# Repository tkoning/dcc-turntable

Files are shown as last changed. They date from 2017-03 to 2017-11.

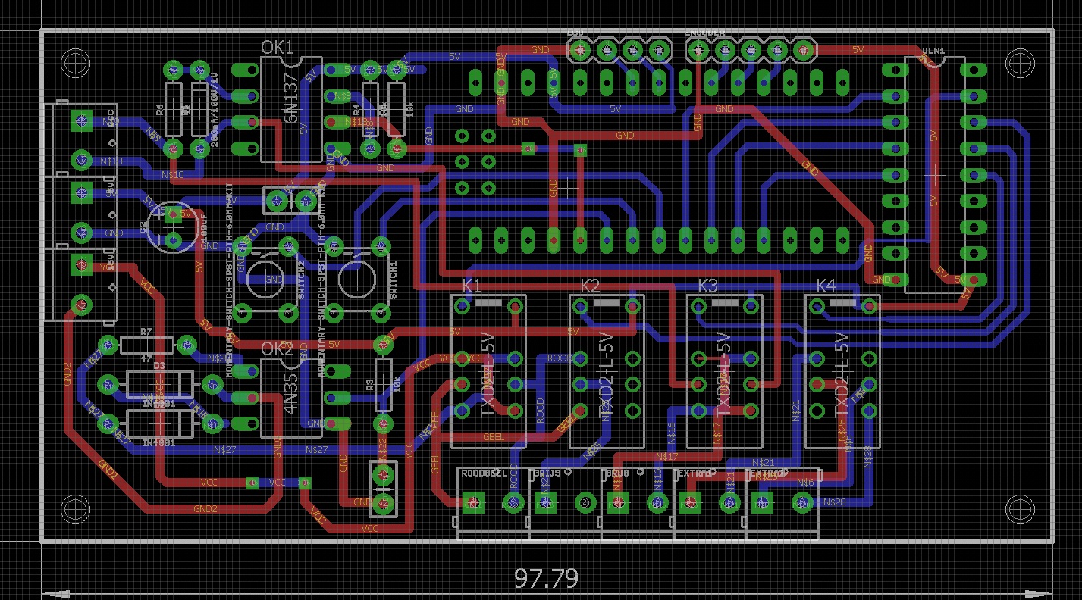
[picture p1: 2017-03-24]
print draaischijf decoder3.jpg

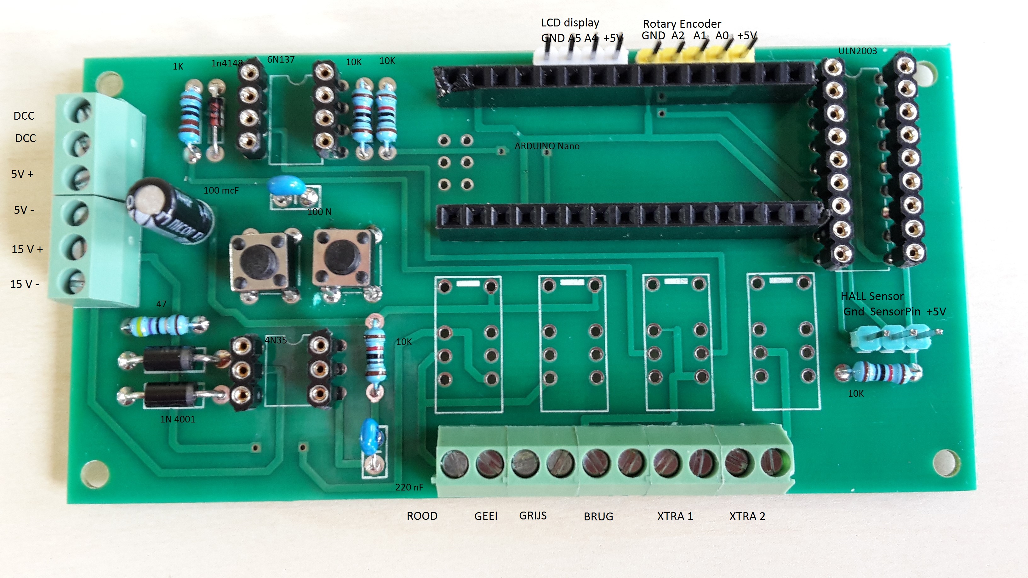
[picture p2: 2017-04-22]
legenda print.jpg

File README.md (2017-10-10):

# dcc-turntable
DCC control of a fleischmann turntable

Digital control of a fleischmann turntable can be achieved with an arduino nano

No modification of the original turntable is needed.
The turntable is controlled by four relays, 

DCC input is by means of the standard mynabay optocoupler circuit.
Manual Control is by means of a rotary encoder and an LCD display.

For indexing of the fleischmann turntable a power sensing circuit is used.
A seperate relais can be used to "flip" the polarity of the turntable brige.

code is annotated in dutch.

the turntable can be seen  in action on youtube.

https://www.youtube.com/watch?v=R1SMiSs2mZU

https://www.youtube.com/watch?v=gE1vPq5jKME

https://www.youtube.com/watch?v=S2jX1PM-Gi4

Schematic of the decoder is in the repository.

New software version 6 : position of bridge is retained at arduino shutdown by setting eeprom parameter in code

erratum : relay's must de mounted on the bottomside of the printed circuit board due to a design mistake regarding polarity of the relay coil.  Increase resitor r6 (dcc optocoupler circuit to 4,7 k)

I have noticed the fleischmann turntable electric engine to be unreliable. Especialy when cold the engine can cause short circuits
A new software version (vs10) cuts the power after a 3 second period
For this to work the positive power line has to be connected via the spare connecors of the aux1 relais

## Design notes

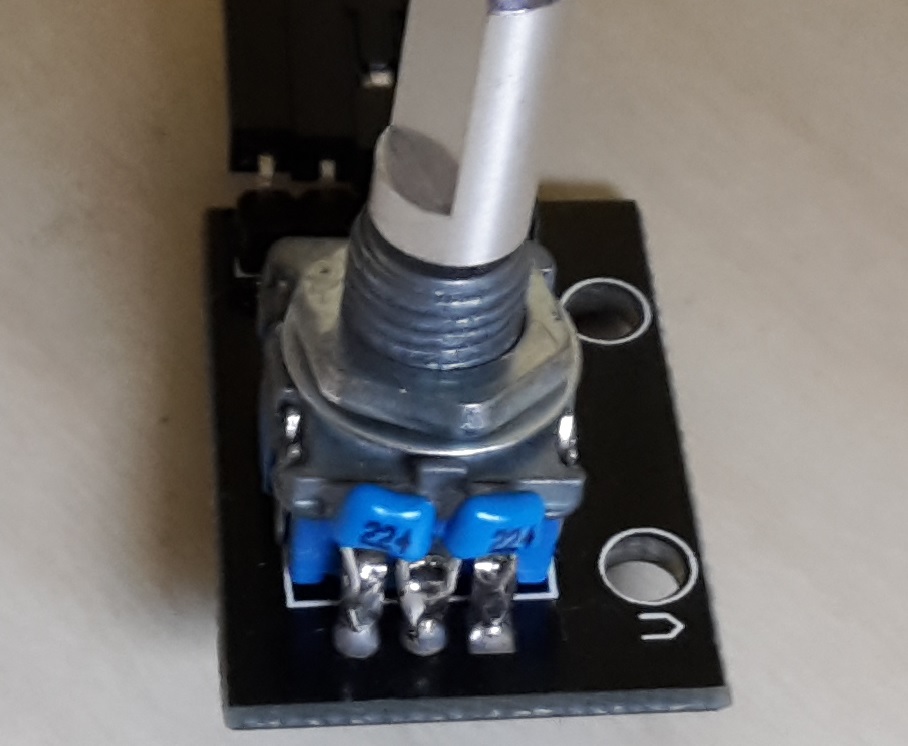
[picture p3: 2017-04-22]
encoder.jpg

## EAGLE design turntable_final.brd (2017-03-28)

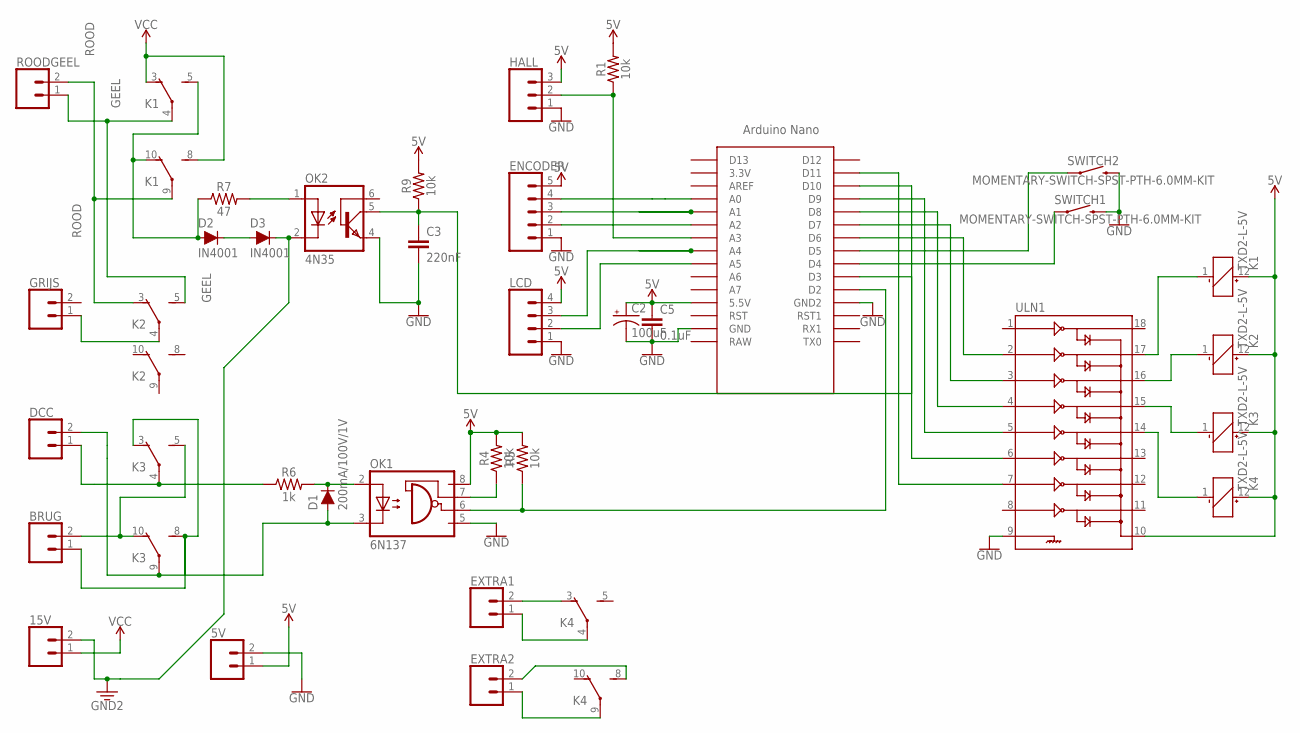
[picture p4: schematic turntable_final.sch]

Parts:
5V, 15V: CONN_023.5MM_LOCK; SCREWTERMINAL-3.5MM-2_LOCK
BRUG: CONN_023.5MM_LOCK; SCREWTERMINAL-3.5MM-2_LOCK
C2: 100uF; CPOL-RADIAL-2.5MM-5MM
C3: 220nF; CAP-PTH-SMALL-KIT
C5: 0.1uF; CAP-PTH-SMALL-KIT
D1: 200mA/100V/1V; DIODE-1N4148
D2, D3: IN4001; DIODE-1N4001
DCC: CONN_023.5MM_LOCK; SCREWTERMINAL-3.5MM-2_LOCK
ENCODER: CONN_05; 1X05
EXTRA1, EXTRA2: CONN_023.5MM_LOCK; SCREWTERMINAL-3.5MM-2_LOCK
GRIJS: CONN_023.5MM_LOCK; SCREWTERMINAL-3.5MM-2_LOCK
HALL: CONN_03; 1X03
K1, K2, K3, K4: TXD2-L-5V; TXD2
LCD: CONN_04; 1X04
OK1: 6N137; DIL08
OK2: 4N35; DIL06
R1, R4, R5, R9: 10k; AXIAL-0.3
R6: 1k; AXIAL-0.3
R7: 47; AXIAL-0.3
ROODGEEL: CONN_023.5MM_LOCK; SCREWTERMINAL-3.5MM-2_LOCK
SWITCH1, SWITCH2: MOMENTARY-SWITCH-SPST-PTH-6.0MM-KIT; TACTILE_SWITCH_PTH_6.0MM_KIT
U$1: NANO
ULN1: ULN2803DIP; DIL18

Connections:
5V: 5V.1, C2.1 (+), C5.1, ENCODER.5, HALL.3, K1.12 (+), K2.12 (+), K3.12 (+), K4.12 (+), LCD.4, OK1.8 (VCC), R1.P$2 (2), R4.P$2 (2), R5.P$2 (2), R9.P$2 (2), U$1.5V (5.5V), ULN1.10
GEEL: K1.4, K2.5 (S), ROODGEEL.1
GND: 5V.2, C2.2 (-), C3.2, C5.2, ENCODER.1, HALL.1, LCD.1, OK1.5 (GND), OK2.4 (EMI), SWITCH1.3 (2), SWITCH2.3 (2), U$1.GND, U$1.GND1 (GND2), ULN1.9
GND2: 15V.2, D3.C, OK2.2 (C)
unnamed: HALL.2, R1.P$1 (1), U$1.A3
unnamed: K3.1 (-), ULN1.15
unnamed: K1.1 (-), ULN1.17
unnamed: ENCODER.3, U$1.A1
unnamed: EXTRA2.1, K4.9
unnamed: K4.1 (-), ULN1.14
unnamed: OK1.7 (VE), R4.P$1 (1)
unnamed: DCC.1, K3.4, R6.P$1 (1)
unnamed: D1.A, DCC.2, K3.9, OK1.3 (C)
unnamed: ENCODER.4, U$1.A0
unnamed: K2.1 (-), ULN1.16
unnamed: OK1.6 (VO), R5.P$1 (1), U$1.D2
unnamed: D1.C, OK1.2 (A), R6.P$2 (2)
unnamed: ENCODER.2, U$1.A2
unnamed: BRUG.2, K3.5 (S), K3.10 (O)
unnamed: BRUG.1, K3.3 (O), K3.8 (S)
unnamed: D2.C, D3.A
unnamed: U$1.D10, ULN1.6
unnamed: OK2.1 (A), R7.P$2 (2)
unnamed: EXTRA1.2, K4.3 (O)
unnamed: C3.1, OK2.5 (COL), R9.P$1 (1), U$1.D3
unnamed: SWITCH1.1, U$1.D4
unnamed: SWITCH2.1, U$1.D5
unnamed: GRIJS.1, K2.4
unnamed: EXTRA1.1, K4.4
unnamed: D2.A, K1.5 (S), K1.10 (O), R7.P$1 (1)
unnamed: EXTRA2.2, K4.8 (S)
unnamed: U$1.D9, ULN1.5
unnamed: U$1.D8, ULN1.4
unnamed: U$1.D7, ULN1.3
unnamed: U$1.D6, ULN1.2
unnamed: LCD.3, U$1.A4
unnamed: LCD.2, U$1.A5
unnamed: U$1.D11, ULN1.7
ROOD: K1.9, K2.3 (O), ROODGEEL.2
VCC: 15V.1, K1.3 (O), K1.8 (S)

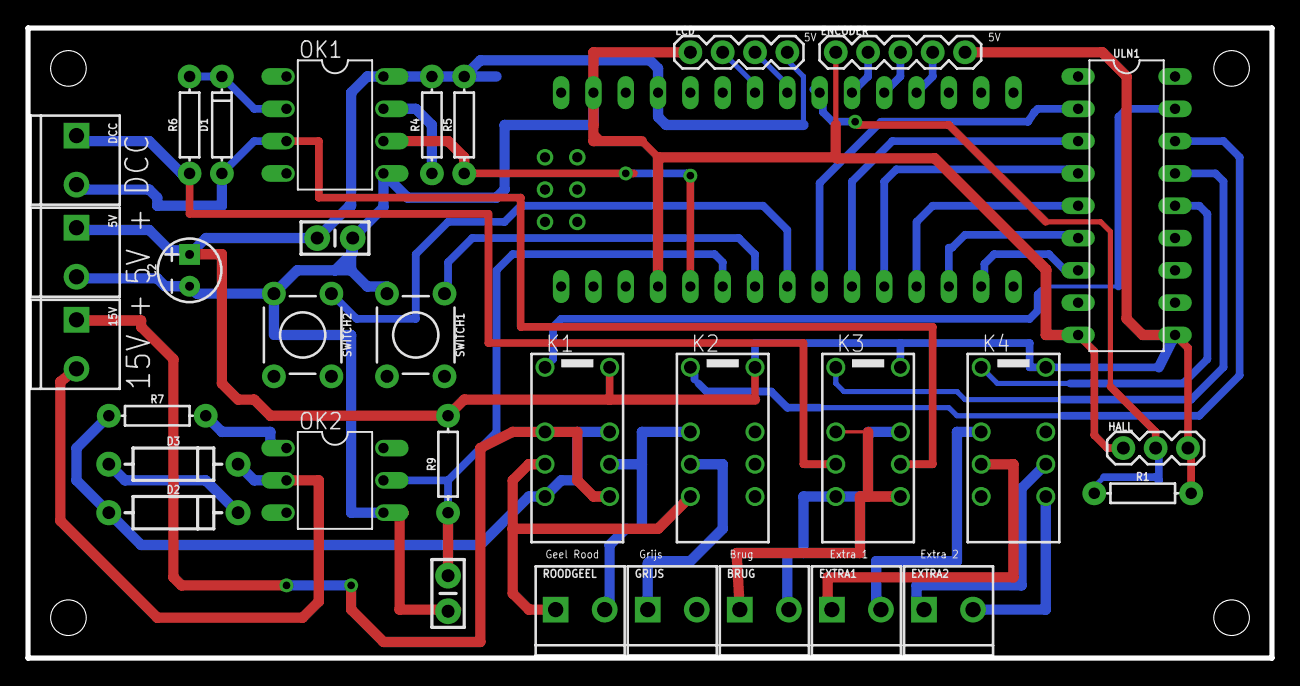
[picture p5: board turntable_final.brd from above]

Board: 2 copper layers, 97.8 x 49.5 mm, 33 parts (0 on the bottom side), 40 nets.

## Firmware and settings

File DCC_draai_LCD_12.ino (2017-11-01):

/*
  //////////////////////////////////////////////////////////////////////////////////////////////////////////////////////
  Arduino DCC Turntable control

  Basis idee  geef korte puls op het locking relais, de draaischijf gaat draaien
  als de draaischijf 1 positie gedraait heeft, stopt de stroom door de motor automatisch
  dit genereert een overgang van laag naar hoog op de motor sense pin
  Gebruik dit event om te bepalen hoeveeel afslagen er gedraaid is en genereer eventueel een nieuwe puls

  versie DCC_draai_lcd10
    inbouwen DCC stuurelementen, eenvoudige koppeling tussen DCC en draaischijf gemaakt
    onderstening van commando'ga naar track nr , + 1 track, -1 track, 180 graden draai
    ondersteuning LCD display
    ondersteuning nieuwe hardware setup met relais sturing via ULN 2803
    aanpassingen tbv nieuw print layout
    gebruik van het EEprom geheugen, de draaischijf onthoudt op welke track de brug stond als het programma wordt afgesloten
    nulling subroutine door het gelijktijdig indrukken van beide print schakelaars
    puls op het aux relais bij het bereiken van de eindpositie
    syntax aanpassingen, variable naamgeving verbeterd
    nog ongeteste beveiliging tegen overbelasting mbv timer in de draairoutine en in main loop
    keuze "nullen" of EEProm geheugen bij het opstarten


  In Rocrail met Xpressnet interface liggen de adressen 4 lager dan de standaard LDT adressen dus basis is 221 ipv 225
  Dit moet worden aangepast met de offset constante
  De Rocrail commando's zijn geinverteerd (instellenin in Rocrail zelf)
  Rocrail genereert 2 commando's een draairichting en een afslagnummer  De draairichting is overbodig en wordt niet gebruikt

  Rotary encoder read example
   https://www.circuitsathome.com/mcu/reading-rotary-encoder-on-arduino/
   niet interupt gebaseerd, afhankelijk van snelheid in de loop
   gebonden aan a0 en a1

  Original DCC sketch : Arduino DCC solenoid Control  Author: Ruud Boer - January 2015
  Adapted for turntable control with LDT protocol Dick Koning feb 2017, echter de nummering van de sporen is conform RocRail

  The DCC signal is optically separated and fed to pin 2 (=Interrupt 0). Schematics: www.mynabay.com
  Many thanks to www.mynabay.com for publishing their DCC monitor and -decoder code.

  Aangepast aan nieuwe motor  (draairichting omgekeerd, tijdconcstante verkleind)


  TODO break statement tijdens daai
  TODO calibratie algoritme

  //////////////////////////////////////////////////////////////////////////////////////////////////////////////////////
*/

#include <DCC_Decoder.h>            // Mynabay DCC library
#define kDCC_INTERRUPT 0

#include <LiquidCrystal_I2C.h>
#include <EEPROM.h>

LiquidCrystal_I2C lcd(0x27, 16, 2); // set the LCD address to 0x27 for a 16 chars and 2 line display

// Pindefinities

const byte dccPin =    2;       // aansluiting DCC signaal
const byte cSense =    3;       // curent sense motoraandrijving
const byte richting =  6;       // Arduino Digital I/O pin number  tbv relais sturing
const byte lock =      7;       // relais wat de interne "lock" van de draaischijf aanstuurt
const byte brug =      8;       // ompoolrelais tbv polariteit van de draaibrug
const byte aux =       9;       // hulp relais bv tbv terugmelding

const byte In_1  =     4;       // Arduino Digital I/O pin number  tbv schakelaars
const byte In_2 =      5;

const byte ENC_A =    14;        //A0   encoder pin A
const byte ENC_B  =   15;        //A1   encoder pin B
const byte ENC_SW =   16;        //A2   encoder switch pin
const byte ledPin =   13;        //ledPin

#define ENC_PORT PINC

// Globale variabelen

int teller = 0;                      // teller is het aantal afslagen dat de schijf moet draaien
int track = 0;                       // actuele afslag waar de draaischijf zich bevindt
int target = 0;                      // doel waarnaar naar toe gedraaid moet worden
byte brugrelais = 0;                 // ompoolrelais draaibrug  Normaal=0 ( NC aansluitingen)  Geinverteerd =1  C aansluitingen
boolean led =     0;

const int EEadres = 100;             // EEadres wordt gebruikt om de track positie vd brug te bewaren
const int EEbrug =  150;             // EEbrug wordt gebruikt om de "stand" van het brugrelais op te slaan
byte EEvalue  =       0;

const boolean aan =    1;
const boolean uit  =   0;
const boolean eeprom = 1;               // eeprom 1 opslag in eeprom,  eeprom  0 geen opslag

const unsigned long pulsDuur = 1500;    // pulsDuur geeft aan hoelang de puls default duurt  Moet iets korter zijn dan de tijd die nodig is voor 1 stap
const unsigned long safeDuur = 3500;    // als de motor langer loopt dan safeDuur stopt de draaischijf automatisch


//////////////////////////////////////////////////////////////////////////////////////////////////////////////////////
// Invulvelden tbv DCC sturing

const int keerA = 12;                 // keerA en keerB zijn de grenzen voor het ompolen van de brug polariteit
const int keerB = 36;

const byte maxaccessories = 6;        // The number of "LDT command" adressen you want to control with this Arduino
const byte offset = 0;                // Offset tov originele LDT adressen  Bij gebruik Xpressnet/ multimouse offset = 4 anders offset = 0

//////////////////////////////////////////////////////////////////////////////////////////////////////////////////////

typedef struct
{
  int               address;          // Address to respond to
  byte              output;           // State of accessory: 1=on, 0=off   rood /groen in wissel commando
  int               track;            // turntable tracknumber
  int               track2;           // turntable track number
  boolean           finished;         // finished : 0=busy 1= ready for next command
  boolean           activate;         // start verwerking commando
  unsigned long     offMilli;         // for internal use
  unsigned long     durationMilli;    // for internal use  "busy periode"

}
DCCAccessoryAddress;
DCCAccessoryAddress accessory[maxaccessories];

//////////////////////////////////////////////////////////////////////////////////////////////////////////////////////
// DCC packet handler
//////////////////////////////////////////////////////////////////////////////////////////////////////////////////////
void BasicAccDecoderPacket_Handler(int address, boolean activate, byte data)
{
  // Convert NMRA packet address format to human address
  address -= 1;
  address *= 4;
  address += 1;
  address += (data & 0x06) >> 1;

  boolean enable = (data & 0x01) ? 1 : 0;

  for (int i = 0; i < maxaccessories; i++)
  {
    if ( address == accessory[i].address )
    {
      accessory[i].activate = 1;
      if ( enable ) {
        accessory[i].output = 1;
      }
      else {
        accessory[i].output = 0;
      }
    }
  }
} // END BasicAccDecoderPacket_Handler


//////////////////////////////////////////////////////////////////////////////////////////////////////////////////////
// Initialization: COPY - PASTE the structure as many times as you have commands and fill in the values you want.
//////////////////////////////////////////////////////////////////////////////////////////////////////////////////////

void ConfigureDecoderFunctions() // The amount of accessories must be same as in line 95 above!
{
  accessory[0].address = 226 - offset; // basisadres LDT =225, eerste commando 226     Voor Multimaus + rocrail  adres -4 invoeren
  accessory[0].track = 0;             // output 0 adres
  accessory[0].track2 = 0;            // output 1 adres    LDT : 226 1 draai 180 graden
  accessory[0].finished = 1;          // Do not change this value
  accessory[0].activate = 0;          // Do not change this value
  accessory[0].output = 0;            // Do not change this value
  accessory[0].durationMilli = 250;

  accessory[1].address = 227 - offset;
  accessory[1].track = 0;             // output 0 adres    LDT : 227 0 draai 1 positie CW
  accessory[1].track2 = 0;            // output 1 adres    LDT : 226 1 draai 1 positie CCW
  accessory[1].finished = 1;          // Do not change this value
  accessory[1].activate = 0;          // Do not change this value
  accessory[1].output = 0;            // Do not change this value
  accessory[1].durationMilli = 250;

  accessory[2].address = 229 - offset;
  accessory[2].track = 0;             // output 0 adres    LDT : 229 ga naar spoor 1
  accessory[2].track2 = 4;            // output 1 adres    LDT : 229 ga naar spoor 2
  accessory[2].finished = 1;          // Do not change this value
  accessory[2].activate = 0;          // Do not change this value
  accessory[2].output = 0;            // Do not change this value
  accessory[2].durationMilli = 250;

  accessory[3].address = 230 - offset;
  accessory[3].track = 6;             // output 0 adres    LDT : 230 ga naar spoor 3
  accessory[3].track2 = 8;           // output 1 adres    LDT : 230 ga naar spoor 4
  accessory[3].finished = 1;          // Do not change this value
  accessory[3].activate = 0;          // Do not change this value
  accessory[3].output = 0;            // Do not change this value
  accessory[3].durationMilli = 250;

  accessory[4].address = 231 - offset;
  accessory[4].track = 24;            // output 0 adres    LDT : 231 ga naar spoor 5
  accessory[4].track2 = 36;           // output 1 adres    LDT : 231 ga naar spoor 6
  accessory[4].finished = 1;          // Do not change this value
  accessory[4].activate = 0;          // Do not change this value
  accessory[4].output = 0;            // Do not change this value
  accessory[4].durationMilli = 250;

  // basisadres LDT =225, eerste commando is programeerstand hier gebruikt als reset, toekomst calibratie oid
  accessory[5].address = 225 - offset;
  accessory[5].track = 0;             // output 0 adres    reset track en target naar 0  moet nog iets in om dat ogv sensor te doen
  accessory[5].track2 = 0;            // output 1 adres    reset track en target naar 0  moet nog iets in om dat ogv sensor te doen
  accessory[5].finished = 1;          // Do not change this value
  accessory[5].activate = 0;          // Do not change this value
  accessory[5].output = 0;            // Do not change this value
  accessory[5].durationMilli = 250;

} // END ConfigureDecoderFunctions



//////////////////////////////////////////////////////////////////////////////////////////////////////////////////////

void setup()
{
  unsigned long timer;
  DCC.SetBasicAccessoryDecoderPacketHandler(BasicAccDecoderPacket_Handler, true);
  ConfigureDecoderFunctions();
  DCC.SetupDecoder( 0x00, 0x00, kDCC_INTERRUPT );


  //-------( Initialize Pins so relays are inactive at reset)----
  digitalWrite(richting, uit);
  digitalWrite(lock, uit);
  digitalWrite(brug, uit);
  digitalWrite(aux, uit);


  //---( THEN set pins as outputs )----
  pinMode(richting, OUTPUT);
  pinMode(lock, OUTPUT);
  pinMode(brug, OUTPUT);
  pinMode(aux, OUTPUT);
  pinMode(ledPin, OUTPUT);
  delay(500); //Check that all relays are inactive at Reset

  pinMode(In_1, INPUT_PULLUP);
  pinMode(In_2, INPUT_PULLUP);
  pinMode(cSense, INPUT);
  pinMode(dccPin, INPUT_PULLUP);              //Interrupt 0 with internal pull up resistor (can get rid of external 10k)
  pinMode(ENC_A, INPUT_PULLUP);
  pinMode(ENC_B, INPUT_PULLUP);
  pinMode(ENC_SW, INPUT_PULLUP);

  digitalWrite(ledPin, LOW);                 //turn off Arduino led at startup
  digitalWrite(aux, aan);                    //schakel het aux relais aan ( draaischijf motorstroom is uit)

  lcd.init();
  lcd.backlight();
  lcd.setCursor(0, 0);
  lcd.print("ArduTurn LCD12");
  lcd.setCursor(0, 1);
  lcd.print("Dick Koning 2017");

  timer = millis() + 2000;
  while (timer > millis())                  // als je bij het opstarten de rotary encoder indrukt ga je naar de default instelling van de brug
  {
    if (digitalRead(ENC_SW) == LOW)
    {
      delay(10);
      if (digitalRead(ENC_SW) == LOW)       // simpele debounce
      {
        EEPROM.write(EEadres, 0);
        EEPROM.write(EEbrug, 0);
      }
    }
  }

  if (eeprom)
  {
    EEvalue = EEPROM.read(EEadres);          // lees het laatst gebruikte "tracknummer" uit de EEprom
    if (EEvalue > 47) EEvalue = 0;           // default staat er 255 in de EEProm
    track = EEvalue;
    target = track;                          // als je deze regel weghaalt draait de draaischijf bij het opstarten altijd naar spoor 0


    brugrelais = EEPROM.read(EEbrug);
    if (brugrelais > 1) brugrelais = 0;

    digitalWrite(brug, brugrelais);
    digitalWrite (ledPin, brugrelais);
    digitalWrite(aux, uit);

  }
  lcd.clear();
  lcdprint();

} //--(end setup )---


//////////////////////////////////////////////////////////////////////////////////////////////////////////////////////
// Main loop
//////////////////////////////////////////////////////////////////////////////////////////////////////////////////////

void loop()
{
  static unsigned long auxTimer = 0;          // hulpvariable tbv aux relais
  static boolean auxActive = 0;

  // target gewenste afslag
  // track actuele afslag
  // teller aantal slagen
  // clockwise(1) : clockwise  clockwise(0) : counter clockwise rotatierichting

  leesDCC();                // genereert een gewenst afslag nummer
  pushButton();             // genereert een gewenst afslag nummer
  settrack();               // selectie mechanisme mbv encoder

  if (target > track)
  {
    teller = target - track;
    if (teller <= 24) {
      clockwise(0);

      while (teller > 0) {   // niet definitief gebruiken, blokkeert alles
        draai(0);
      }
    }
    else
    {
      teller = 48 - teller ;
      clockwise(1);

      while (teller > 0) {   // niet definitief gebruiken, blokkeert alles
        draai(1);
      }
    }
    if (eeprom)
    {
      EEvalue = byte(track);
      EEPROM.write(EEadres, EEvalue);
    }
    auxActive = 1;
    auxTimer = millis() + 250;
    digitalWrite (aux, aan);
  }

  if (target < track)
  {
    teller = track - target;

    if (teller <= 24) {
      clockwise(1);

      while (teller > 0) {   // niet definitief gebruiken, blokkeert alles
        draai(1);
      }
    }
    else
    {
      teller = 48 - teller ;
      clockwise(0);

      while (teller > 0) {   // niet definitief gebruiken, blokkeert alles
        draai(0);
      }
    }
    if (eeprom) {
      EEvalue = byte(track);
      EEPROM.write(EEadres, EEvalue);
    }
    auxActive = 1;
    auxTimer = millis() + 250;
    digitalWrite (aux, aan);
  }


  if (auxActive) {
    if (millis() > auxTimer ) {
      digitalWrite (aux, uit);
      auxActive = 0;
    }
  }

  // experimentele storingsroutine

  if (!digitalRead(cSense))                                // cSense is laag : er loopt stroom door de motor   Hier moet je mischien nog iets van een debounce in zetten
  {
    delay(safeDuur);                                       // wacht een veilige periode en test opnieuw
    if (!digitalRead(cSense))                              // stroomgebruik gaat door ->>> uitschakelen schijf
    {
      lcd.clear();
      lcd.setCursor(0, 0);
      lcd.print("Storing ");
      lcd.setCursor(0, 1);
      lcd.print("Power OFF ");

      digitalWrite(aux, aan);                              //  het aux relais schakelt de stroom naar de draaischijf uit
      while (digitalRead(ENC_SW) == HIGH) {                //  endless loop tot rotary encoderschakelaar geactiveerd wordt
        delay(500);
        led = !led;
        digitalWrite(ledPin, led);
      }
      digitalWrite(aux, uit);
      lcdprint();
    }
  }
}


//////////////////////////////////////////////////////////////////////////////////////////////////////////////////////
// DCCLoop
//////////////////////////////////////////////////////////////////////////////////////////////////////////////////////

void leesDCC()
{
  static int addr = 0;                    // Static variable assignment alleen bij startup. Waarde persisteert als de functie verlaten wordt

  DCC.loop(); // Loop DCC library



  if (accessory[addr].finished && accessory[addr].activate)    //event wordt 1 maal getriggerd daarna verplichte pauze
  {
    accessory[addr].finished = 0;
    accessory[addr].offMilli = millis() + accessory[addr].durationMilli;

    if (accessory[addr].output == 1)
    {
      switch (accessory[addr].address) {
        case (225-offset):   //calibratie draaischijf
          dreset();
          break;
        case (226-offset):   // halve draai  LDT 226
          target = track - 24;
          if (target < 0) target = target + 48;
          break;
        case (227-offset):  // 1 step clockwise LDT 227
          target = track - 1;
          if (target < 0) target = target + 48;
          break;

        default:
          target = (accessory[addr].track2);
          break;
      }

    }
    else // output=0
    {
      switch (accessory[addr].address) {
        case (225-offset):   // calibratie draaischijf
          dreset();
          break;
        case (226-offset):   // halve draai  LDT 226
          target = track + 24;
          if (target >= 48) target = target - 48;
          break;

        case (227-offset):  // 1 step  counter clockwise
          target = track + 1 ;
          if (target >= 48) target = target - 48;
          break;

        default:
          target = (accessory[addr].track);
          break;
      }
    }
    lcdprint();
  }


  if ((!accessory[addr].finished) && (millis() > accessory[addr].offMilli))    // blokkade want commando herhaalt zich zelf
  {
    accessory[addr].finished = 1;
    accessory[addr].activate = 0;
  }
  if ( ++addr >= maxaccessories ) addr = 0;
  // Adres wordt opgehoogd tbv volgde cyclus. Staat  aan het einde van de subroutine om bij een break uit de loop de eerstvolgende keer dat de loop geactiveerd wordt eerst finished te resetten.
}


//////////////////////////////////////////////////////////////////////////////////////////////////////////////////////
// Aansturing van de draaischijf
//////////////////////////////////////////////////////////////////////////////////////////////////////////////////////

void draai(bool brichting)
{
  static bool pulsBusy = false;            // pulsBusy is de variable die aangeeft dat het interne draaischijf locking relais geactiveerd is
  static unsigned long pulsTimer = 0;      // pulsTimer is de teller die meeloopt met de duur van de relais puls
  static unsigned long safeTimer = 0;      // safeTimer is de teller die meeloopt gedurende de periode dat de motor van de draaischijf loopt

  // teller is het aantal afslagen dat de schijf moet draaien    Globale variable
  // richting is de variabele die aangeeft welke kant de draai opgaat  Procedure Parameter

  if (!pulsBusy) {
    pulsTimer = millis() + pulsDuur;
    safeTimer = millis() + safeDuur;
    pulsBusy = true;
    digitalWrite(lock, aan);
    delay(10);                              // probeersel geef het relais even tijd
  }
  else {
    if ( millis() > pulsTimer)
    {
      digitalWrite(lock, uit);              // de default pulsperiode is voorbij

      if (digitalRead(cSense)) {            // cSense is hoog : er loopt geen stroom door de motor
        delay (2);                          // debounce tbv 100hz "PWM"
        if (digitalRead(cSense)) {          // cSense is hoog : er loopt geen stroom door de motor
          
          teller = teller - 1;
          pulsBusy = false;
          if (brichting) {                     // richting 1=clockwise   0=counterclockwise
            track = track - 1;
            if (track < 0) track = track + 48;
            lcdprint();
            if (track == keerA || track == keerB) {
              brugrelais = !brugrelais;       // statement voor ompolen railrelais.  Kies de sporen ogv de layout
              dbrug(brugrelais);
            }
          }
          else
          {
            track = track + 1;
            if (track >= 48) track = track - 48;
            lcdprint();
            if (track == keerA || track == keerB) {
              brugrelais = !brugrelais;      // statement voor ompolen railrelais  Kies de sporen ogv de layout
              dbrug(brugrelais);
            }
          }
        }
      }
    }
    if ( millis() > safeTimer)                              // de draaistap duurt langer dan de veilige periode
    {
      digitalWrite (aux, aan);                              //  het aux relais schakelt de stroom naar de draaischijf uit
      lcd.clear();
      lcd.setCursor(0, 0);
      lcd.print("Storing ");
      lcd.setCursor(0, 1);
      lcd.print("Power OFF ");

      while (digitalRead(ENC_SW) == HIGH) {                 //  endless loop tot rotary encoder schakelaar geactiveerd wordt
        delay(500);
        led = !led;
        digitalWrite(ledPin, led);
      }
      pulsBusy = false;
      teller = 0;                                          //  stop de draairoutine
      target = track;                                      //  voorkom dat de draairoutine opnieuw wordt opgestart
    }
  }
}
//--(end draairoutine )---





void clockwise(bool on)
{
  if (on) {
    digitalWrite(richting, aan);
  }
  else {
    digitalWrite(richting, uit);
  }
  delay(10);
}

void pushButton()
{
  // invoer dmv druk toetsen  0 = ingedrukt

  if (!digitalRead(In_1)) {
    delay(20);
    if (!digitalRead(In_2)) {                 // als je beide drukknoppen tegelijk indrukt "nul je de schijf"
      dreset();
    }
    else {
      target = track + 1;
      if (target >= 48) target = target - 48;
      lcdprint();
    }
  }
  if (!digitalRead(In_2)) {
    delay(20);
    if (!digitalRead(In_1)) {                 // als je beide drukknoppen tegelijk indrukt "nul je de schijf"
      dreset();
    }
    else {
      target = track - 1;
      if (target < 0) target = target + 48;
      lcdprint();
    }
  }
}
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

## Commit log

2017-03-15 schematic turntable decoder
2017-03-16 prototype decoder
2017-03-16 Revised schematic turntable decoder
2017-03-28 Add files via upload
    Eagle files
    [turntable_final.brd, turntable_final.sch]
2017-08-10 Add files via upload
    Includes additional software to protect against short circuits

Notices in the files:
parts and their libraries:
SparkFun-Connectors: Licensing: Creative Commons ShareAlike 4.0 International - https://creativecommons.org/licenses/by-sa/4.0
